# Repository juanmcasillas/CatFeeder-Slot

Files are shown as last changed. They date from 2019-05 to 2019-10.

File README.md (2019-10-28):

# CatFeeder-Slot

This project builds an automatic feeder for cats (or other small animals). The goal is build a complete, DIY solution,
from the fabrication of the container, to software are electronics. The feeder is managed using a web interface, so you
can configure it from your home network. Doubles as WIFI AP (for standalone operation) or WIFI client (for home network
integration).

This project provides:

1. The fabrication of the container. You 3D print the parts using the STL provided.
2. The software to control the feeder.
3. The electronics schemas to connect all the parts. 

<a href="https://youtu.be/_xY0Vlgl6Cg">Demo video on YouTube</a>

# Table Of Contents

1. [Project Features](#project-features)
2. [3D Printing and Assembly](#3d-printing-and-assembly)
    1. [Prototype](#prototype)
    2. [CatFeeder](#catfeeder)
        1. [Part list to print](#part-list-to-print)
        2. [Printing times](#printing-times)
        3. [Assembly](#assembly)
            1. [Mount the pins in the inner case](#mount-the-pins-in-the-inner-case)
            2. [Screw the base to the inner case](#screw-the-base-to-the-inner-case)
            3. [Mount the axis motor and support](#mount-the-axis-motor-and-support)
            4. [Iron the wires to battery holder](#iron-the-wires-to-battery-holder)
            5. [Build the 90 degree wires](#build-the-90-degree-wires)
            6. [Wiring diagram](#wiring-diagram)
            7. [Mount the UNL2003](#mount-the-unl2003)
            8. [Mount the ESP8266](#mount-the-esp8266)
            9. [Mount the cap](#mount-the-cap)

3. [How to install the Software](#how-to-install-the-software)
    1. [Arduino Board Setup](#arduino-board-setup)
    2. [Configuration options](#configuration-options)
    3. [Download the components to the Board](#download-the-components-to-the-board)
        1. [Check for good compilation](#check-for-good-compilation)
        2. [Download the FileSystem to the board](#download-the-filesystem-to-the-board)
        3. [Download the CatFeeder application to the board](#download-the-catfeeder-application-to-the-board)
4. [Configure CatFeeder](#configure-catfeeder)
    1. [Connect to the AP](#connect-to-the-ap)
5. [Using Catfeeder](#using-catfeeder) 
    1. [Calibration](#calibration)
    2. [Configure Schedules](#configure-schedules)
6. [Additional Notes](#additional-notes)

# Project Features

1. Fully printable container, so you can download the project, start your printer, and print all the parts. The STL are 
ready to print, so the orientation and tolerances are configured and tested.
2. Managed using web interface. Catfeeder provides a WWW server that provides the following capabilities:
    * Network configuration. DCHP / Static / AP operation
    * Calibration
    * NTP client, so we manage the current time.
    * Configuration persistence (SPIFFS).
    * Detailed log of Catfeeder's operation, so you can check what happen.
    * Modern HTML / JS interface, AJAX based operation.
    * Easy, flexible schedule configuration for feeding your pets. No limits on this (only the number of slots).
    * Capable of communicate using a Telegram Bot (Experimental).
3. Cheap to build. Based on standard hardware components:
    * ESP8266 Core on an NodeMCU LoLin v3 development board (about 7€)
    * Stepper motor: 28BYJ48 (5 motors about 6€)
    * Stepper motor driver: ULN2003 (5 drivers mounted on development board about 6€)
    * Printed on PLA
    * Some wiring cable (8 wires)
    * 4 allen screws (13mm)
    * 2 allen screws (6mm)
    * Powered on 4xAA batteries (6V)
    * 1 4xAA battery holder (5 holders about 4€)
    * 4 small screws to support the boards to pins
    * 4 pins to build the power connector
4. Easy of operation:
    * Cap is removable so you can clean / add the meal easily.
    * The shape is designed to be "safe" for your cats. They can't bump it.
    * Schedule the meals using the phone or your computer easily.
    * With 1 meal/day, you can serve a full week.
    * Very quiet operation, due the stepper motor.
    * Can be calibrated easily, using the web interface.

# 3D Printing and Assembly

All the parts are designed on Autodesk Inventor 2019. I provide two models, **CatFeeder** the "production" one, and the **Prototype** useful to develop new features, or test things. Printed on 
a Creality Ender-3 Pro, with generic brand PLA. These are the CURA settings for all the parts printed:

* Layer Height: 0.2
* Wall Thickness: 0.8
* Top/Botton Thickness: 0.8
* Top Layers: 4
* Bottom Layers: 4
* Infill: 20%, Lines
* Printing temperature: 195 ºC (for your PLA brand, may vary)
* Build plate temperature: 70 ºC
* Speed: 40 mm/s
* Cooling: Enable
* Fan Speed: 100%
* Enable supports: Everywhere
* Build Plate adhesion: None

## Prototype

This prototype is not usable to feed pets, buts prints fast, and is used to check some mechannical interfaces (axis, motor coupling, etc.) The prototype is an easy asembly, build from three printed parts:

* Hardware/3DPrinting/Prototype/floor.stl
* Hardware/3DPrinting/Prototype/mottor_support.stl
* Hardware/3DPrinting/Prototype/upper.stl

You also need:

* 6 female-female pin-to-pin cables (4 for motor wires, 1 for vcc, 1 for ground)
* 4 AA batteries
* A battery holder with two male pin soldered (to enable the connection)
* A ESP8266 Board
* Mini-USB Cable (to power the ESP8266 and check the serial debug)

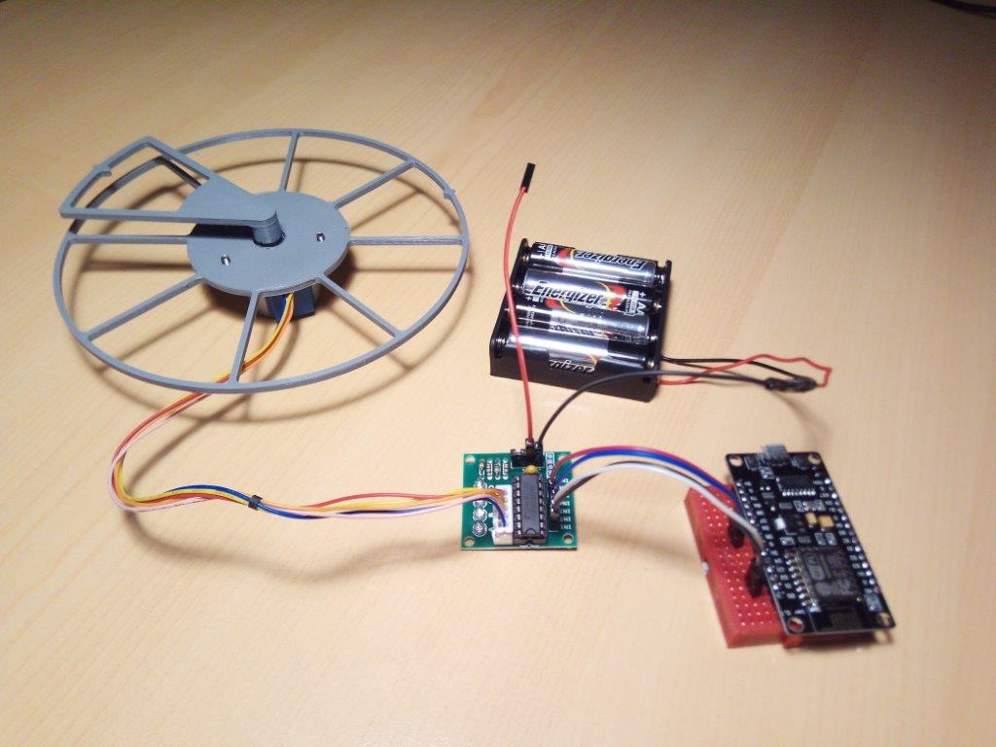
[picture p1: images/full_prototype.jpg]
  

## CatFeeder

This is the production-ready CatFeeder parts. CatFeeder has a diameter of **190mm**, and **650** of height. Each slots size **72mm x 90mm**. It takes some time to print, so be patient.
See the following diagram for more detail about measures.

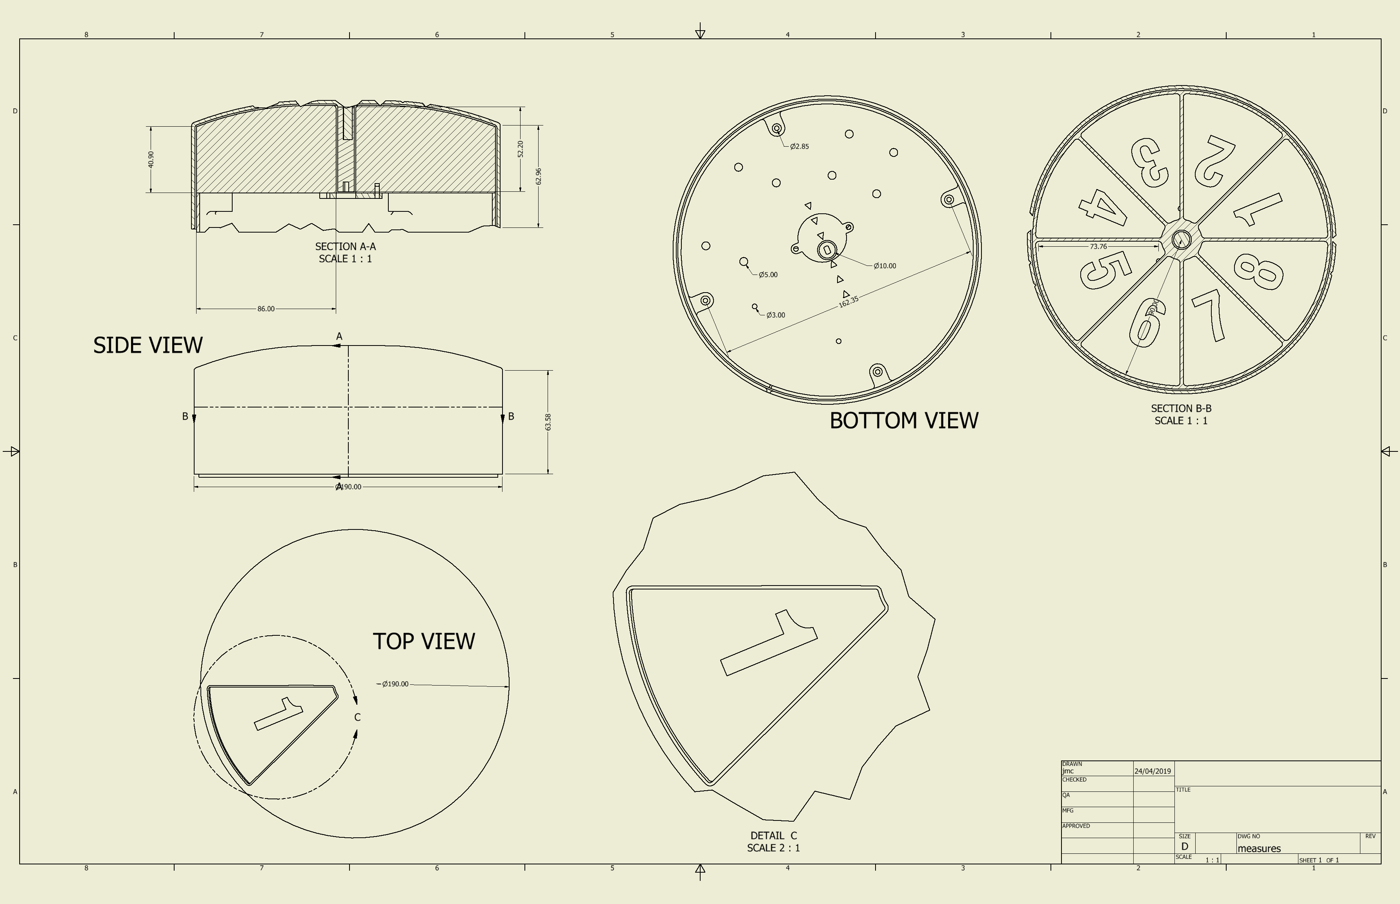
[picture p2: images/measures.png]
  

### Part List to print

You need to print this files (included in the Repo):

* Hardware/3DPrinting/CatFeeder/1x_axis.stl 
* Hardware/3DPrinting/CatFeeder/1x_motor_support.stl  
* Hardware/3DPrinting/CatFeeder/1x_base.stl
* Hardware/3DPrinting/CatFeeder/1x_cap.stl
* Hardware/3DPrinting/CatFeeder/1x_inner_case.stl
* Hardware/3DPrinting/CatFeeder/2x_separator_battery.stl
* Hardware/3DPrinting/CatFeeder/8x_separator.stl

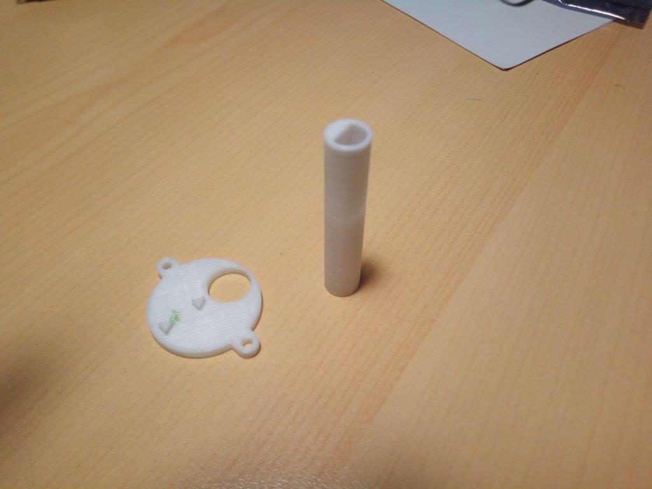
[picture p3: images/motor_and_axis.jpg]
 
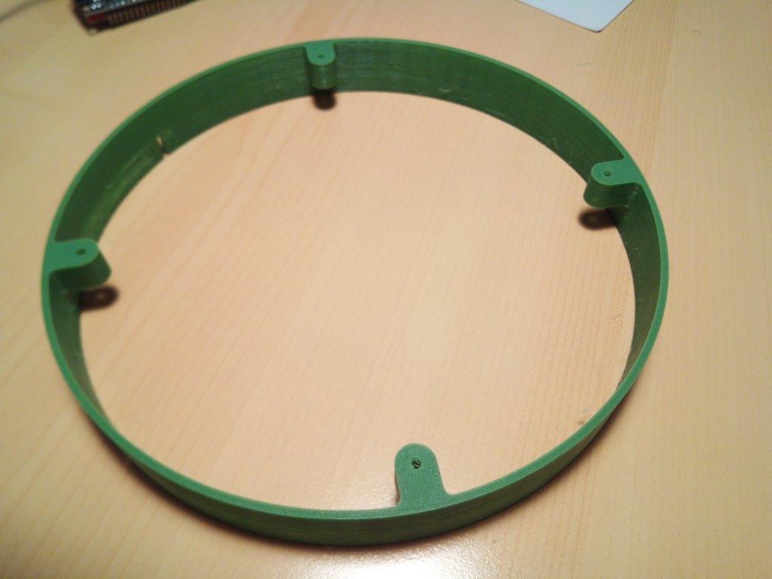
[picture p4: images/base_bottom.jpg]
 
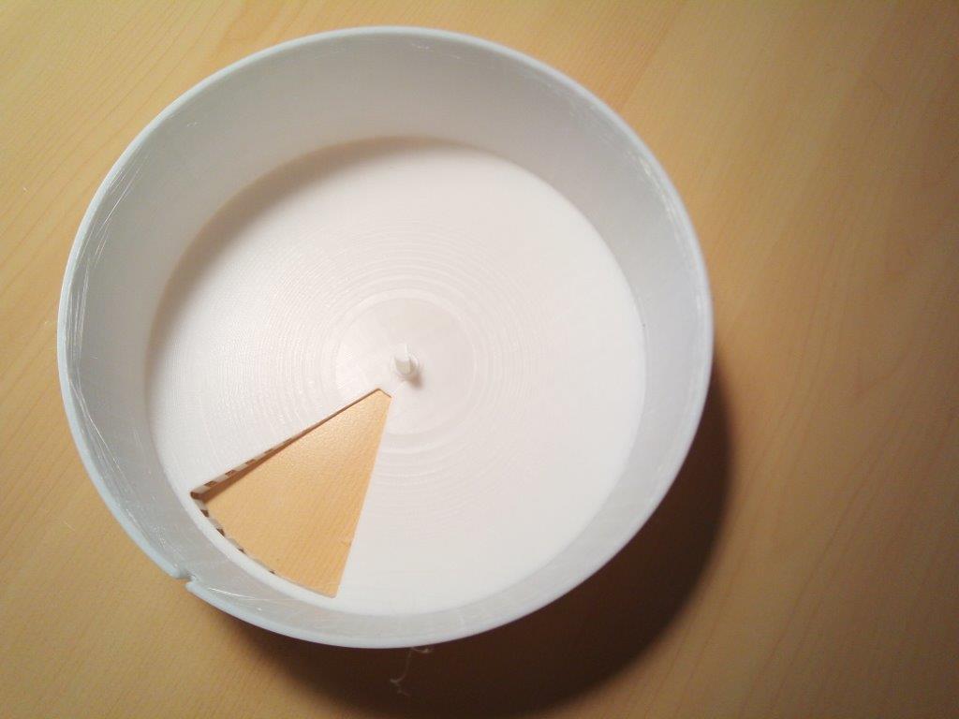
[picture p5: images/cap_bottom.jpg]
 
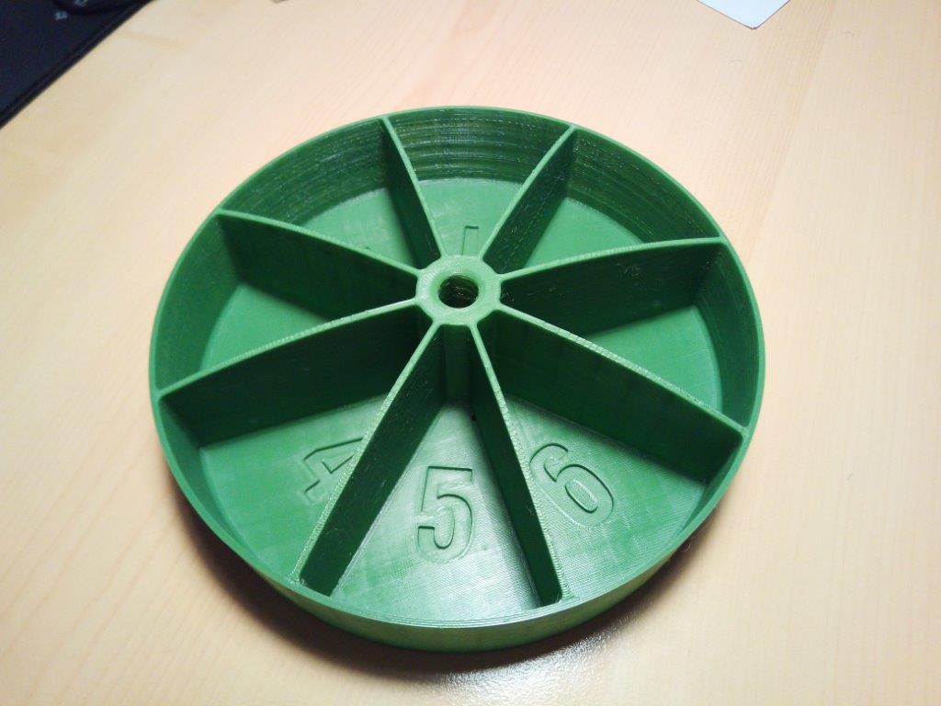
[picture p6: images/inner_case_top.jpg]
 
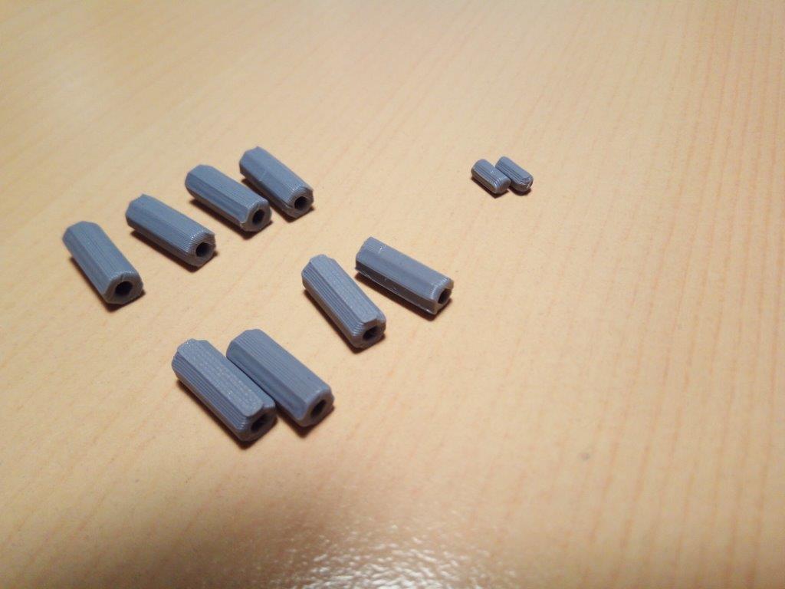
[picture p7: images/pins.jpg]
 

### Printing times

|part name  |cuantity|color|printing time|
|---|---|-----|---:|
|motor axis |1 |white| 00:45|
|base |1 |green| 02:30|
|cap |1 |white| 14:38|
|inner case |1 |green| 16:15|
|motor support |1 |white| 00:30|
|separator_battery|2 |grey | 00:05|
|separator |8 |grey | 00:10|

### Assembly

To assemble the CatFeeder, you need the following:

* All the parts printed
* ESP8266 Core on an NodeMCU LoLin v3 development board
* Stepper motor: 28BYJ48
* Stepper motor driver: ULN2003
* Some wiring cable (10 wires)
* 4 allen screws (13mm)
* 2 allen screws (6mm)
* 4xAA batteries (6V)
* 1 4xAA battery holder
* 1 Micro USB cable to download the firmware
* An allen driver to screw the allen screws (nº 3)
* An Iron to solder the battery holder wires and build the 90 degree wires
* 4 small screws to support the boards to pins

#### Mount the pins in the inner case

Parts:
* Separators (8 big, 2 small)
* Inner Case (bottom side)

Push the pins (separators) in their holes to support the boards. The two small ones are the battery separator (2mm) and the 8 are the ULN2003 holder and ESP9266 holder, that fits in the big holes.
Push gently, and if you found too much resistence, file them lightly using a sharp knife. Also you can glue the pins to the base, but it shouldn't be needed.

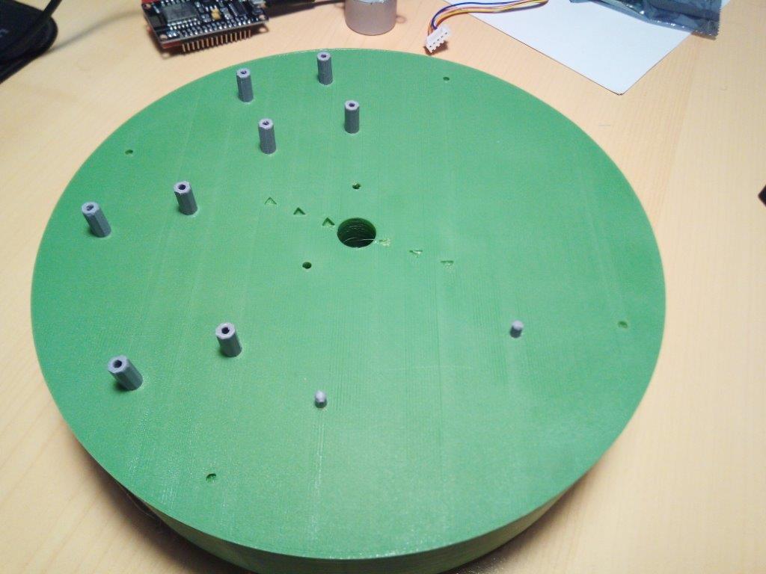
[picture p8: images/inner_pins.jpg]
 

#### Screw the base to the inner case

Parts:
* Inner Case
* Base
* 4 Screws (10mm, allen) 

Using the 4 long screws, screw the base to the inner case. File lightly the holes to ensure smooth fit.

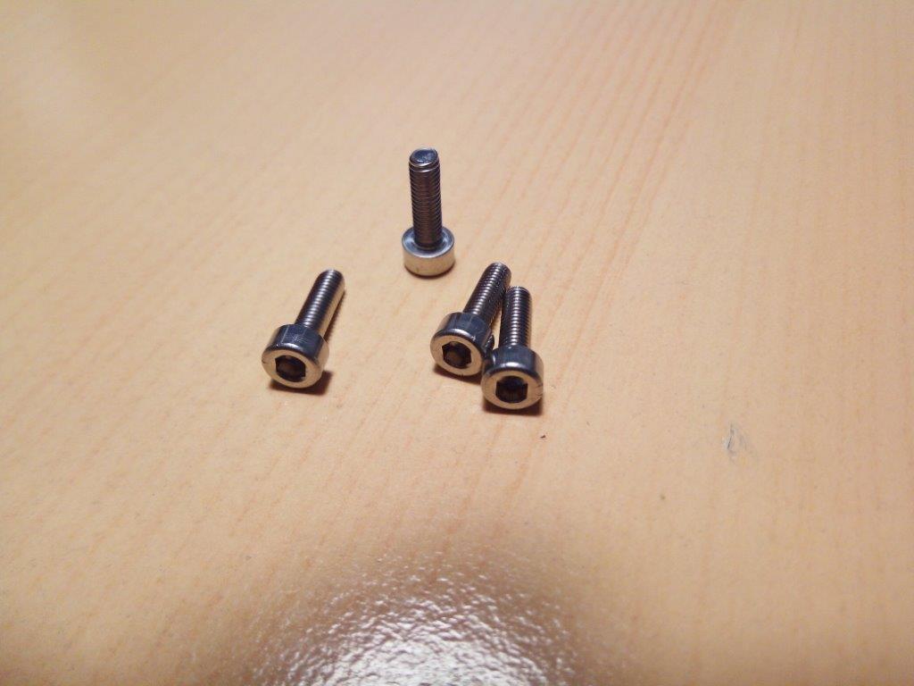
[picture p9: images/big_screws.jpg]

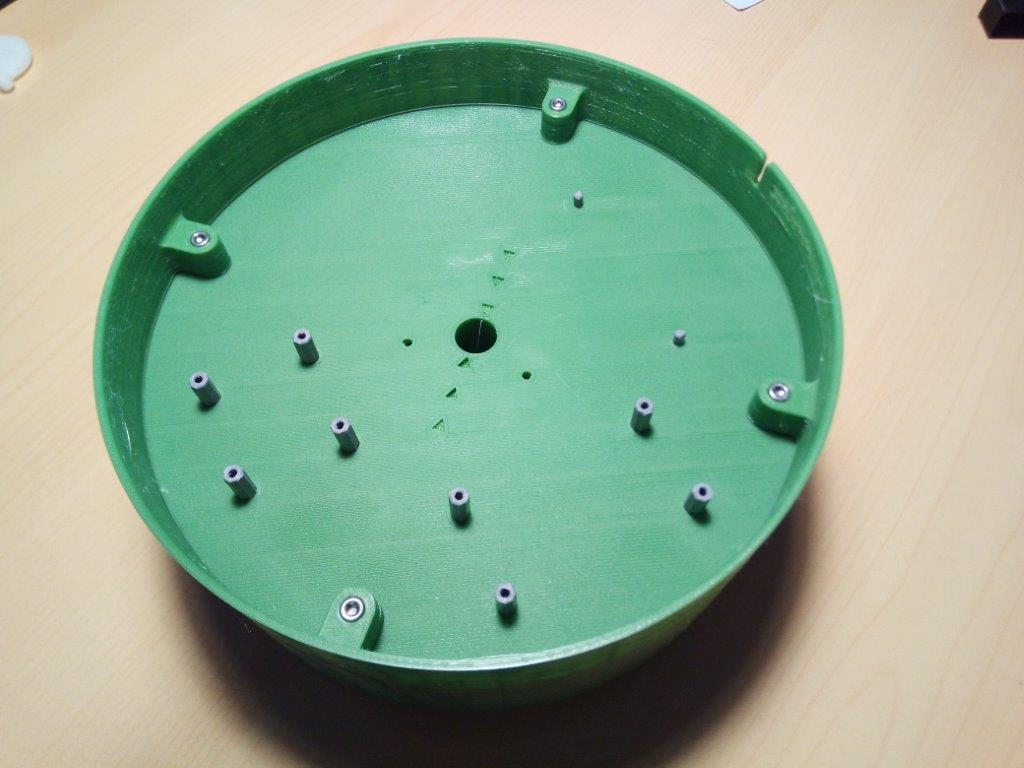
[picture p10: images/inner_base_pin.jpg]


#### Mount the axis motor and support

Parts:
* Motor Axis
* Motor Support
* 2 Screws (6mm, allen)

Push gently the motor into the axis. The axis (long part) has two pockets. One big, one small. In the photo you will see the big one, used to hold the cap. Push firmly but not to hard. It should be fitted
snugly. 

Now, get the motor support, and align it with the inner base (bottom) The protuding triangles are designed to be fitted in the triangle pockets in the inner case. Once fitted the support, screw the motor
to the inner case using the small screws. The support, the motor and the axis only have one way to be mounted.


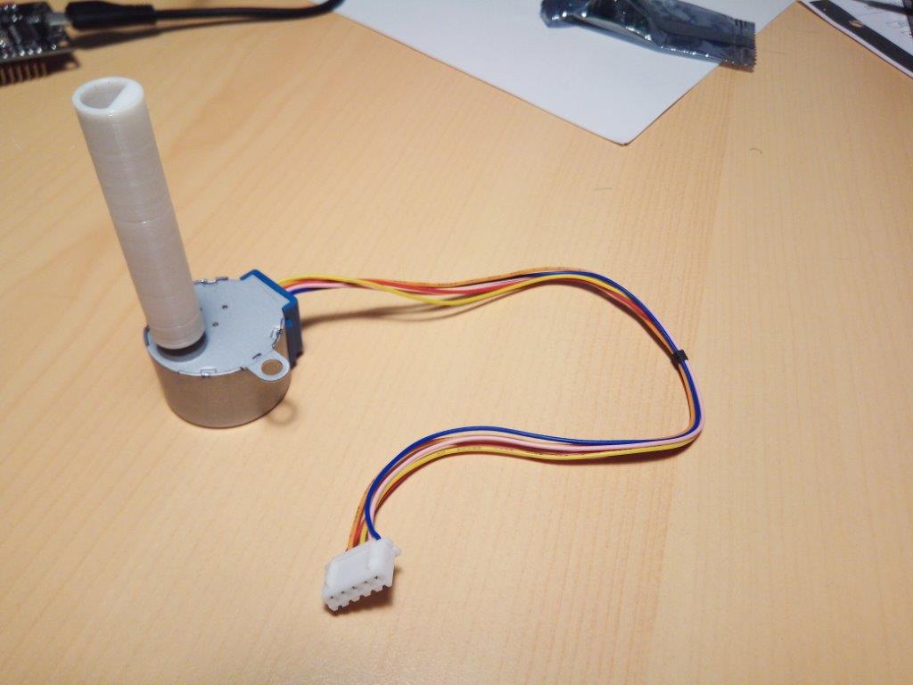
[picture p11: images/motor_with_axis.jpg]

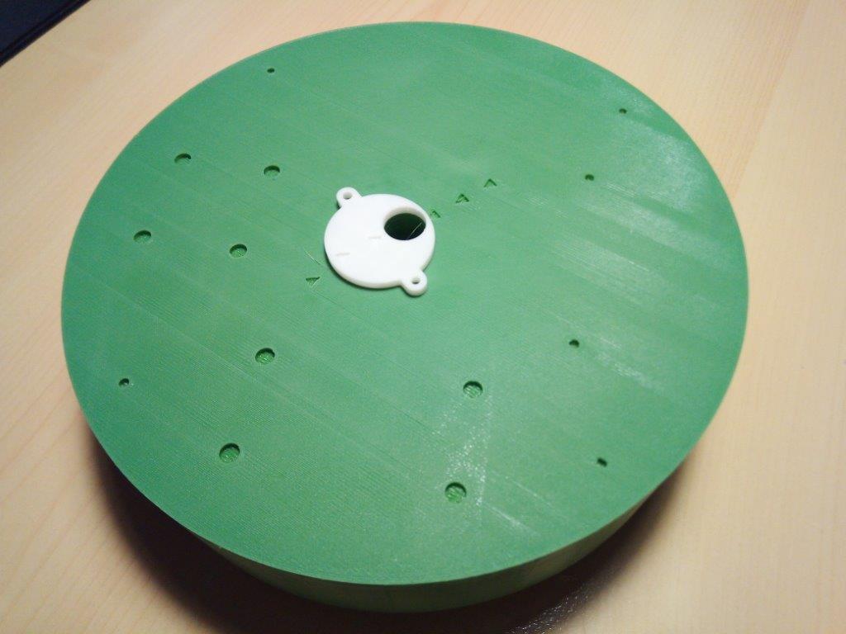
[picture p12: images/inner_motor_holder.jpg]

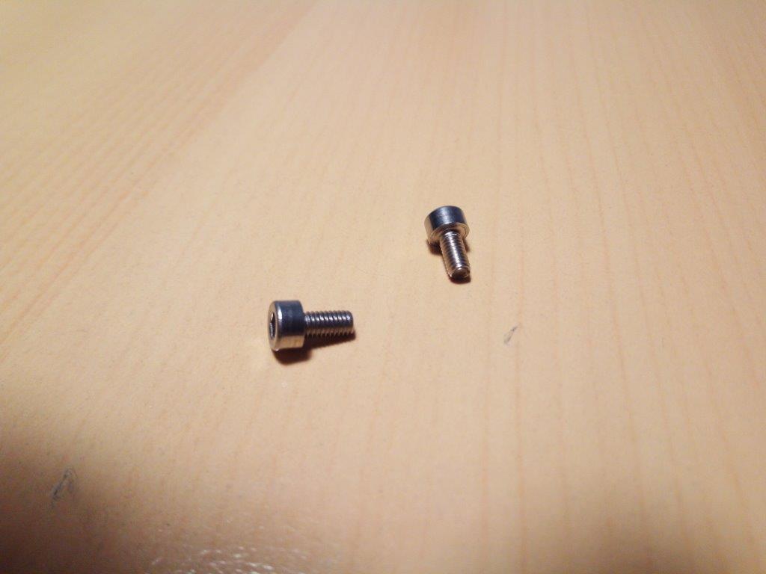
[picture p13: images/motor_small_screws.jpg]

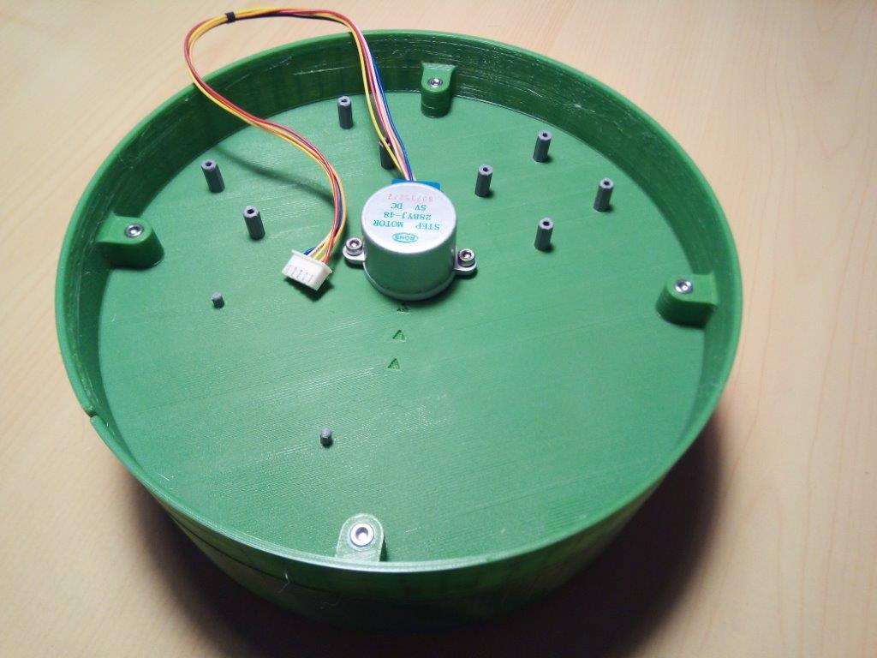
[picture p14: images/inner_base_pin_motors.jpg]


#### Iron the wires to battery holder

Parts:
* Battery Holder
* Two wires (about 10cm each one)
* 4 pins to build the connector
* Iron

First of all, we need to "build" a connector for the power. Get a pin strip as the photo, and split two pairs of pins. Stack them, and iron the pins
together using the wires. You will get something like the connector in the photo.  Then, iron the wires to the battery holder. 
I usually iron the *red* one to the VCC (+) and the *black* to the GND (-).

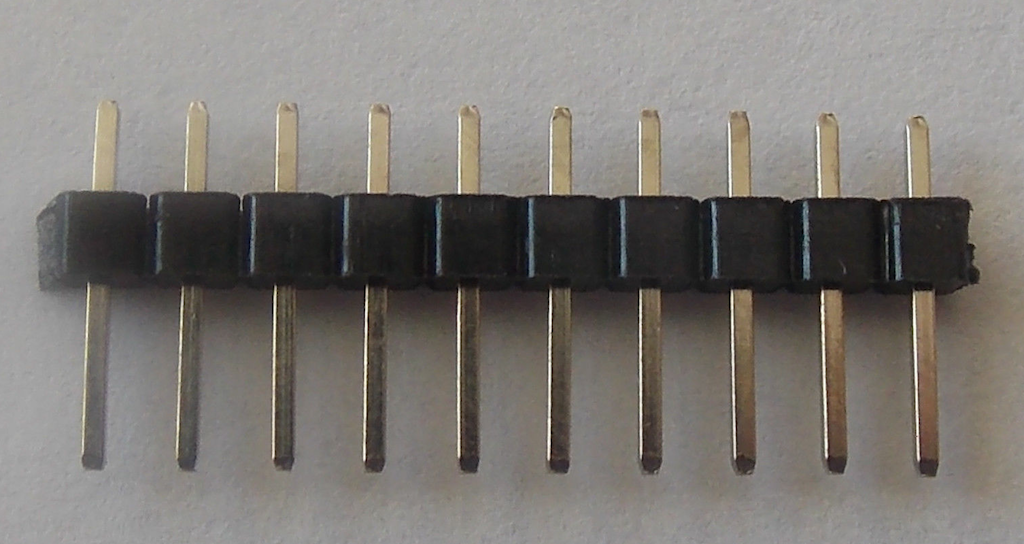
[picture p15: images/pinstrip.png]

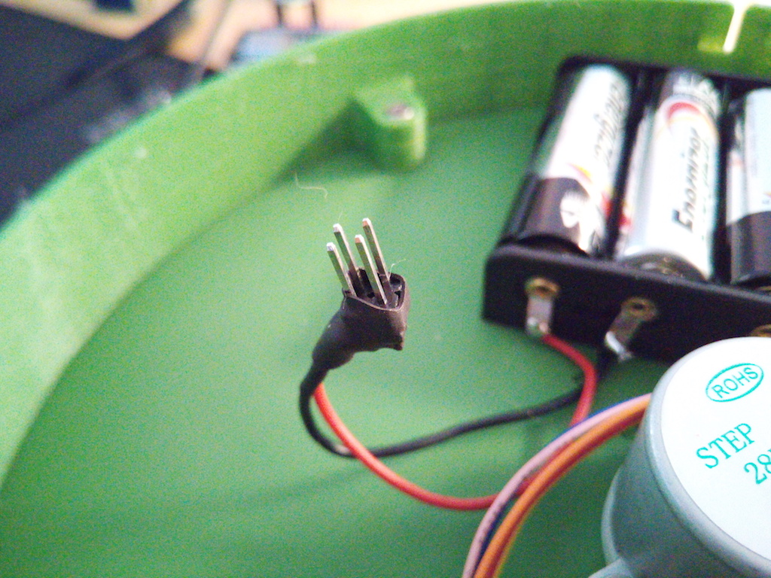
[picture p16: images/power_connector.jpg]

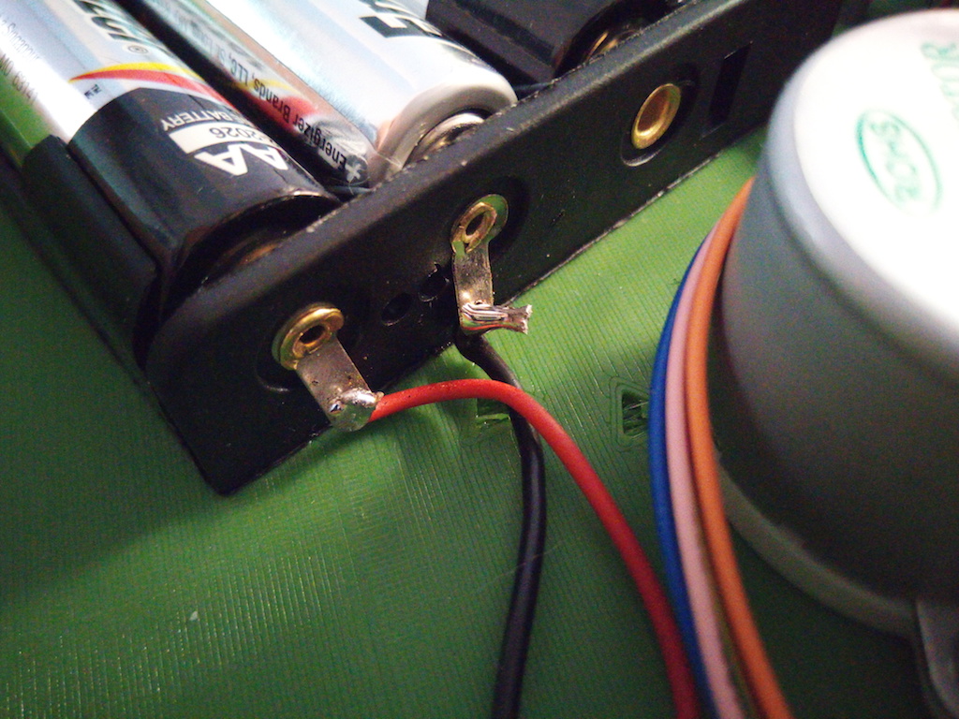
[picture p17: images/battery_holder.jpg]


#### Build the 90 degree wires

Parts:
* Simple female-female connection wires (10)
* Iron
* plier

I want to get a low-profile cat feeder, so I ended using 90 degrees cables to connect the ESP8266 and the UNL2003 motor driver, along the power supply. I get a standard
female-female connection wire, removing the plastic cap (a needle or sharp cutter is useful to extract the plastic cap), add some thermoretractile (while the pin is still
straight) and them, using the pliers, bend the end point to 90 degree. Apply some heat, and you have a 90-degree connection cable done. Repeat 10 times (4 wires for 
motor signals, 2 for power the ESP8266, 2 for power the UNL2003).

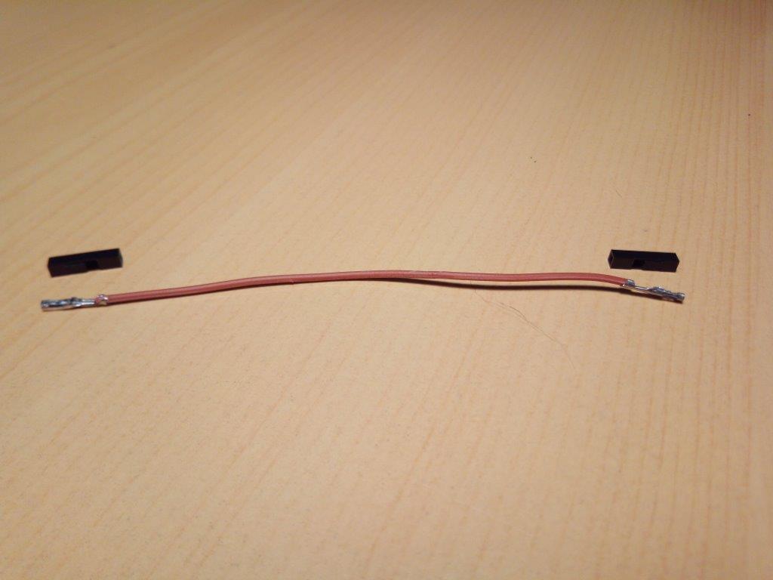
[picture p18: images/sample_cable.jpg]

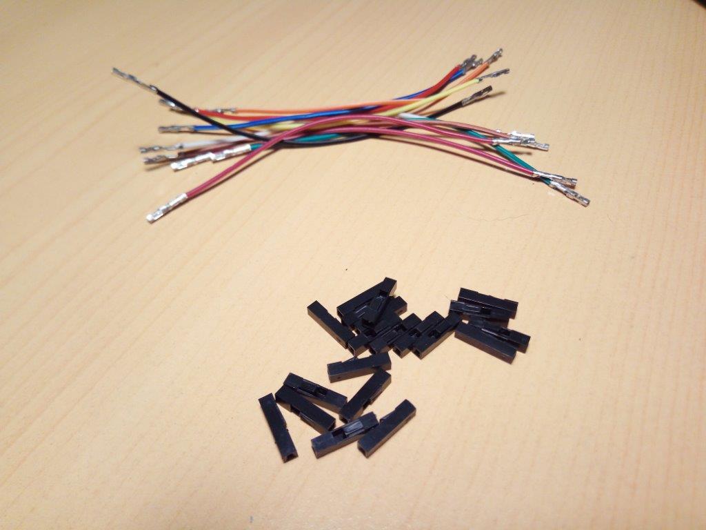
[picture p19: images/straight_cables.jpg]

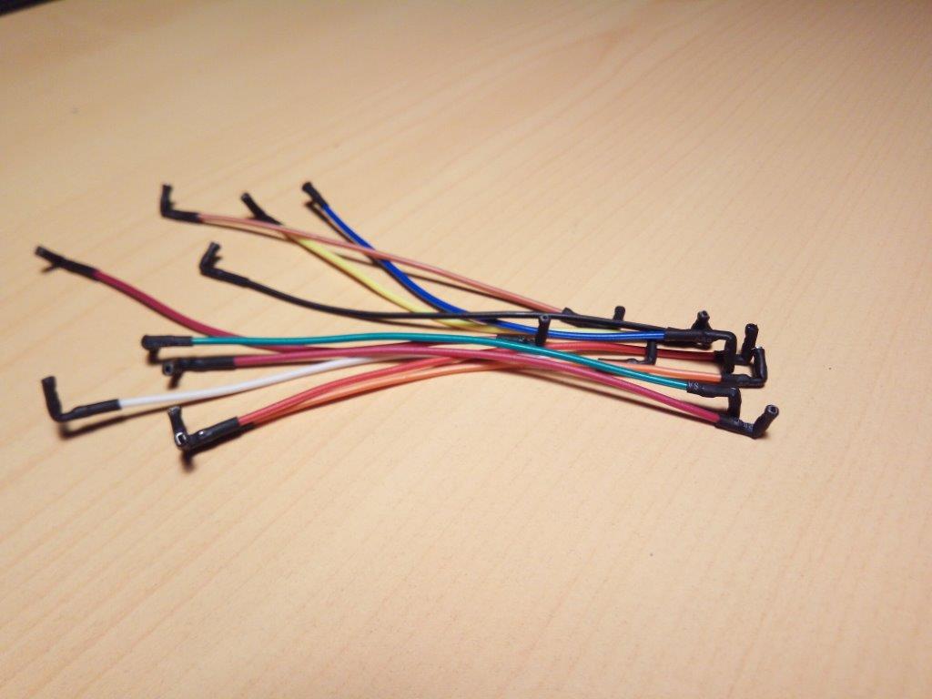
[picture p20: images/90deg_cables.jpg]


#### Wiring diagram

Wiring is easy. Just use the following diagram to connect the wires between power, ESP8266, UNL2003 and the stepper motor. I power the ESP8266 using 6V (4x1.5V) using the
voltage regulator provided by the development board. See the subsections about UNL2003 and ESP8266 for detailed photos. 

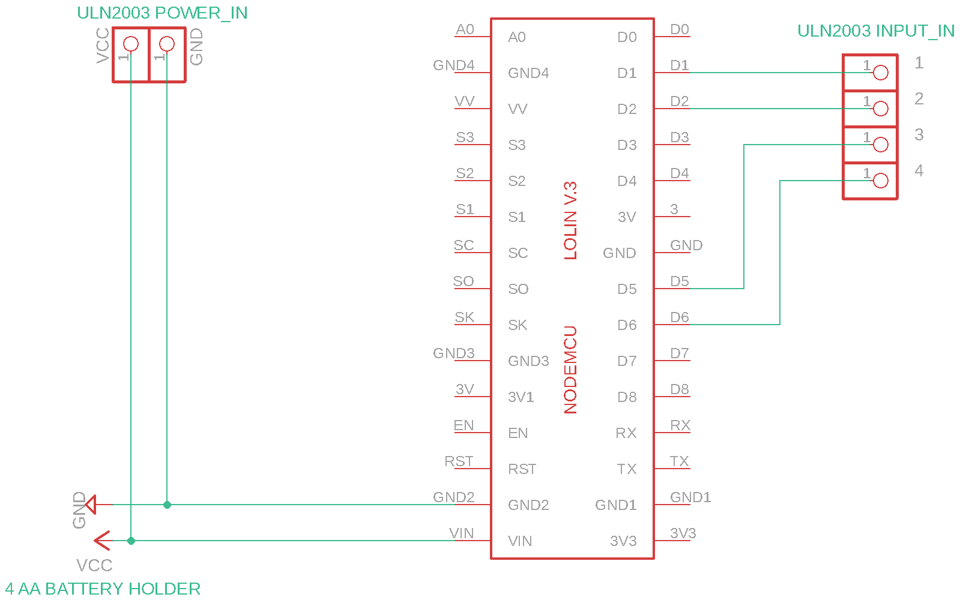
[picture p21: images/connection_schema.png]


#### Mount the UNL2003 

Parts:
* Inner case
* UNL2003 Motor Driver
* 6 wires (4 for signals, 2 for power)
* Motor connector
* 2 small screws

Put the UNL2003 in their separators, and screw it to them using the small screws. I get these screws from iside a VHS video recorder found in the garbage. Plug in the
motor connector in the white connector holder (it has only one valid position to insert it). Last, connect the wires using the following table.

|UNL2003 Name|Color |ESP8266 PIN|
|---|---|---|
|IN1 |Yellow|D1 |
|IN2 |Orange|D2 |
|IN3 |Grey  |D5 |
|IN4  |Blue  |D6 |
|- |White |*power connector black*|  
|+ |Red |*power connector red*|

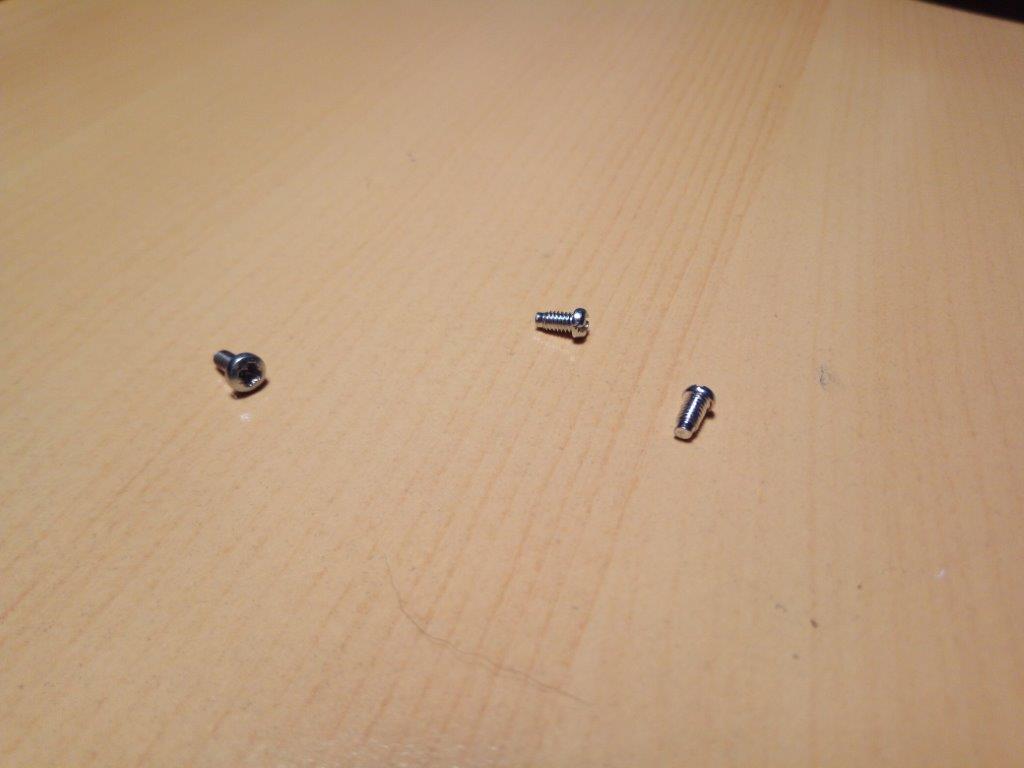
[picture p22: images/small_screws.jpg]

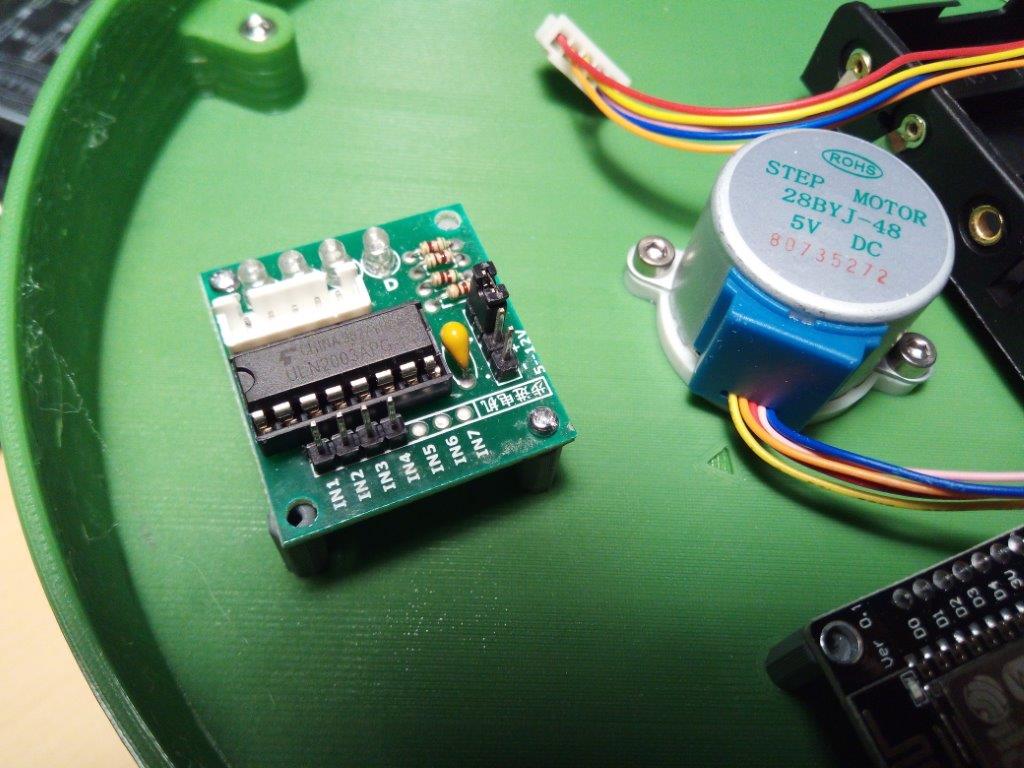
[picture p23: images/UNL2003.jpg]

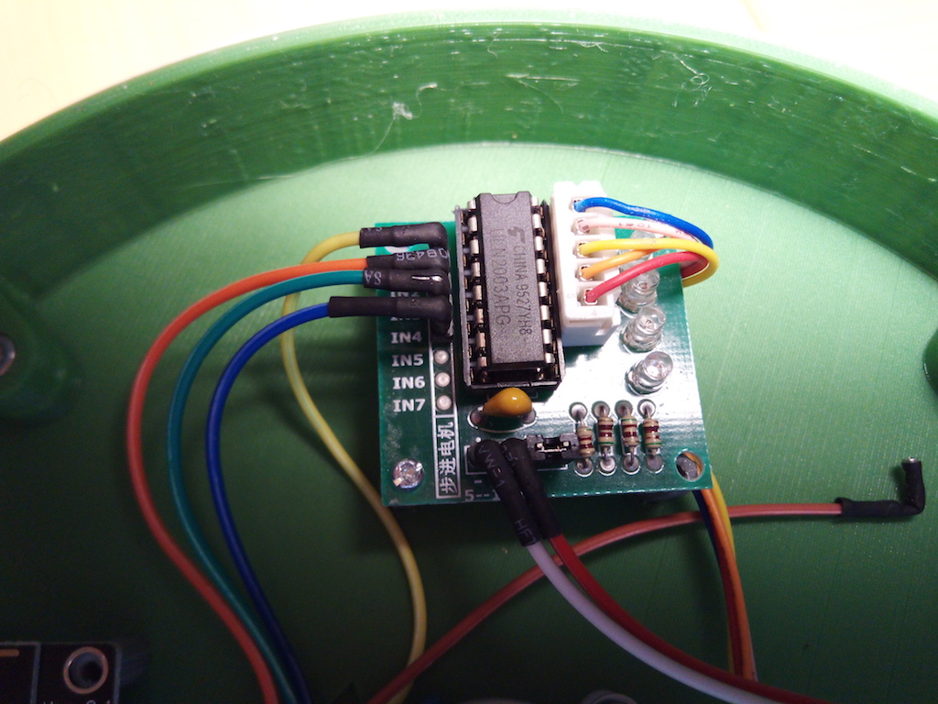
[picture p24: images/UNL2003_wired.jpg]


#### Mount the ESP8266 

Parts:
* Inner case
* ESP8266 
* 4 wires coming from UNL2003
* 2 wires for power
* 2 small screws
* Micro-USB cable

First of all, connect the wires coming from UNL2003 using the previous table. Connect the power cables to the `GND2` (black wire) and `VIN` (red wire) pins, and screw 
it to the separators. Last, plug all the power wires to the battery holder connector. You shold have all connected and ready to go. Don't forget to plug the Micro-USB
cable to the ESP8266 in order to download the filesystem and firwware. The extra, unpluged wire in the photo is due a some test I was doing. Don't take it in mind.

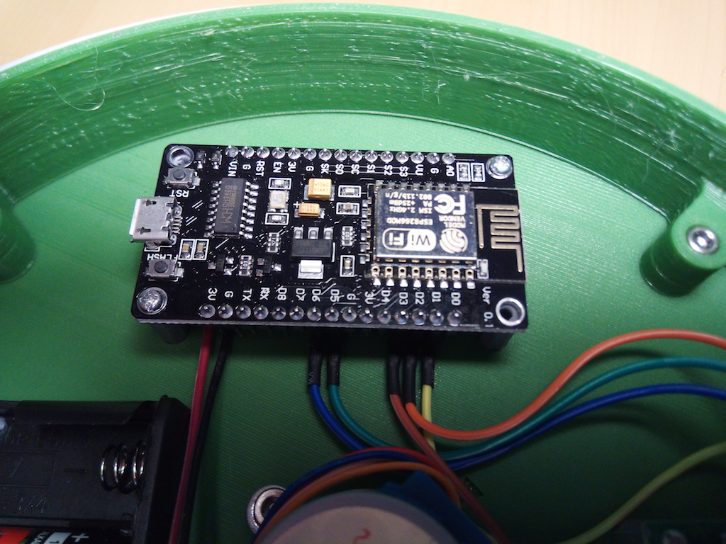
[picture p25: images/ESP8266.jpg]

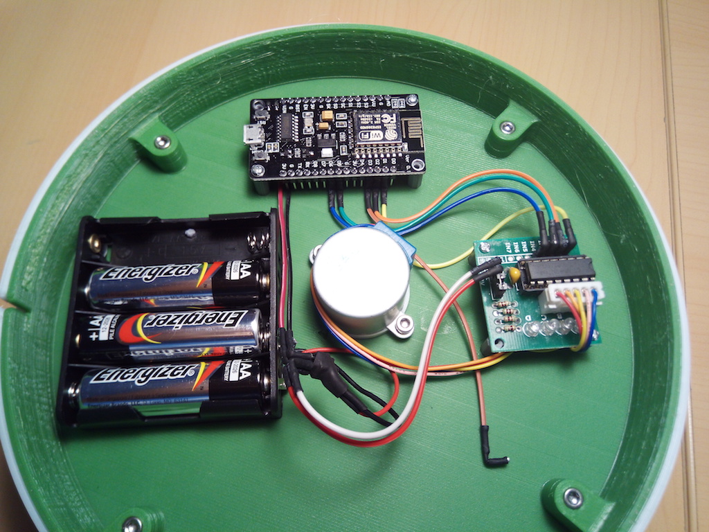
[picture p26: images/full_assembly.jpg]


#### Mount the cap

Parts:
* Cap
* Inner case fully assembled

First of all, remove all the support from the top of the cap. Use a sharp cutter. The cap has an axis that fits in the motor axis. This allows the cap to be removed to
put the food, clean the inner case, etc. The cap fits easily in the axis holder. You are done!.

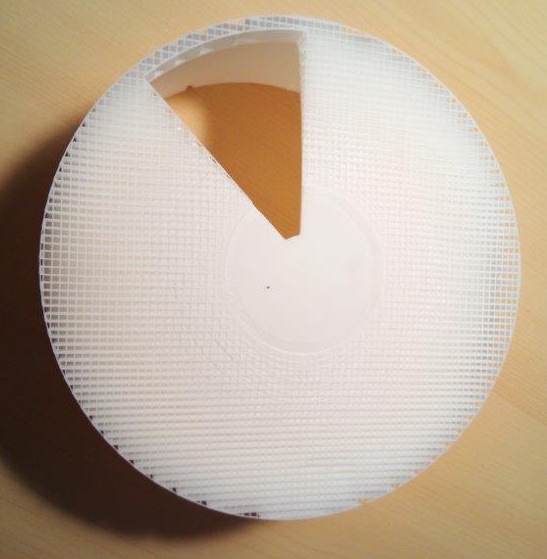
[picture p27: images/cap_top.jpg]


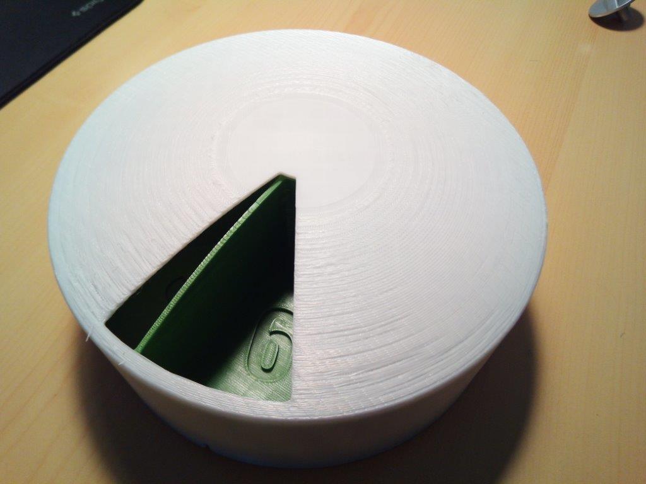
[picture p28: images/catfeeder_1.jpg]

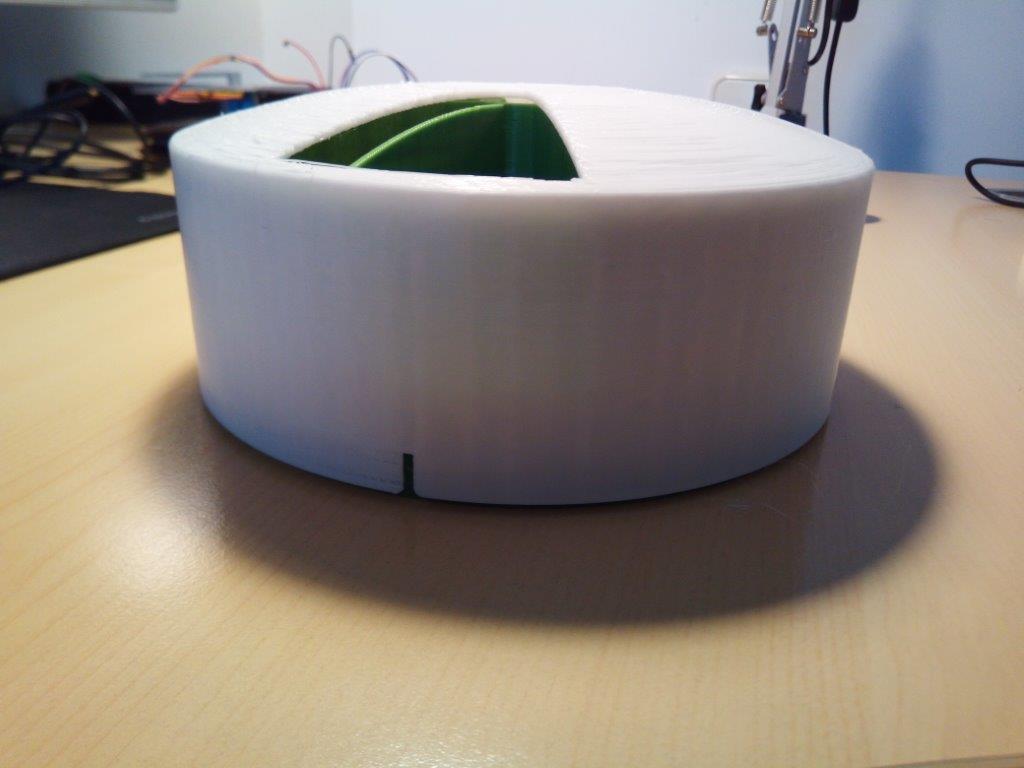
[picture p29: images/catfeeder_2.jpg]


# How to install the Software

CatFeeder uses [FSBrowserNG](https://github.com/gmag11/FSBrowserNG) as webserver. I forked it, to include some new functionality and fix some `delay()` calls that can't be used. You need the following libraries installed in your Arduino `libraries` folder.

* [my FSBrowserNG's fork](https://github.com/juanmcasillas/FSBrowserNG). See [the original page](https://github.com/gmag11/FSBrowserNG) for more info. Depends on:
    * [ArduinoJson-5.x](https://github.com/bblanchon/ArduinoJson/tree/5.x) (the 5.x branch)
    * [ESPAsyncTCP](https://github.com/me-no-dev/ESPAsyncTCP)
    * [ESPAsyncWebServer](https://github.com/me-no-dev/ESPAsyncWebServer)
    * [NtpClient](https://github.com/arduino-libraries/NTPClient)
    * [Time](https://github.com/PaulStoffregen/Time)
* [my Universal-Arduino-Telegram-Bot's fork](https://github.com/juanmcasillas/Universal-Arduino-Telegram-Bot). See [the original page](https://github.com/witnessmenow/Universal-Arduino-Telegram-Bot) for more info.

Then, get the [CatFeeder Repo](https://github.com/juanmcasillas/CatFeederCircular) and compile it using the Arduino IDE.

## Arduino Board Setup

I use a *NodeMCU LoLin v.3 ESP8266* board. You need some things in Arduino IDE in order to work:

* First install the serial driver, if not installed before, for your platform [CH340G Driver](http://www.wch.cn/download/CH341SER_EXE.html)

Then add ESP8266 aditional library:
* Go to `Preferences`, add in `Additional Board Manager URLs` the following URL: [http://arduino.esp8266.com/stable/package_esp8266com_index.json](http://arduino.esp8266.com/stable/package_esp8266com_index.json)
* Restart The Arduino IDE.
* Go to `Tools->Board->Board Manager` and search `ESP8266 by ESP8266 Community` library and install it (I use version `2.5.0`)
* Install the ESP8266FS Flash filesystem tools form Arduino. Uncompress [package](https://github.com/esp8266/arduino-esp8266fs-plugin/releases/download/0.1.3/ESP8266FS-0.1.3.zip) inside `C:\Software\Arduino\tools`
* Install Exception Decoder ESP8266. Not really needed to install the software, but can help you to troubleshoot some things if fail. Uncompress [package](https://github.com/me-no-dev/EspExceptionDecoder/releases/download/1.1.0/EspExceptionDecoder-1.1.0.zip) inside `C:\Software\Arduino\tools`
* Restart the Arduino IDE.

Now, You have to configure the Board options:

* Board: `NodeMCU 1.0 (ESP-12E Module)`
* Upload Speed: `921600` (If you can't connect at this speed, check the cable or select a lower speed)
* CPU Freq: `80 MHz`
* Flash Size: `4M (2M SPIFFS)`. This is importart. If you don't do select that, you can't flash the FileSystem.
* Debug port: `Disabled`
* Debug Level: `None`
* IWIP Variant: `v2 Lower Memory`
* VTables: `Flash`
* Exceptions: `Disabled`
* Erase Flash: `Only Sketch`
* Port: Your USB port.
* Programmer: `AVRISP mkII`

## Configuration options

in `catfeeder.h` you find the following `defines`:
* `#define CATFEEDER_SLOTS 8` number of slots. If you use the provided STL, leave in `8`
* `String CATFEEDER_CONFIG_FILE =  "/catfeeder.json"`. The configuration options.
* `String LOGGER_FILE = "/catfeeder.log". The log file where things are stored.

in `motorstepper.h` you find the pin-to-wire mapping:
* `const int motorPin1 = D1;   // D1  (GPIO14)      IN1     black`
* `const int motorPin2 = D2;   // D2  (GPIO12)      IN2     white`
* `const int motorPin3 = D5;   // D5  (GPIO13)      IN3     blue`  
* `const int motorPin4 = D6;   // D6  (GPIO15)      IN4     red` 

## Download the components to the Board

### Check for good compilation

 First of all, open `catfeedercircular.ino` file in *Arduino IDE* and issue a `Verify` to check that everything compiles (libraries, and so on). When you have a valid compilation, then you should have a log output like this:

 ```
Using library ESP8266WiFi at version 1.0 in folder: /Users/assman/Library/Arduino15/packages/esp8266/hardware/esp8266/2.5.0/libraries/ESP8266WiFi 
Using library Time at version 1.5 in folder: /Archive/Src/Arduino/libraries/Time 
Using library NtpClient at version 2.5.1 in folder: /Archive/Src/Arduino/libraries/NtpClient 
Using library ESPAsyncTCP at version 1.2.0 in folder: /Archive/Src/Arduino/libraries/ESPAsyncTCP 
Using library ESPAsyncWebServer at version 1.2.0 in folder: /Archive/Src/Arduino/libraries/ESPAsyncWebServer 
Using library ESP8266mDNS at version 1.2 in folder: /Users/assman/Library/Arduino15/packages/esp8266/hardware/esp8266/2.5.0/libraries/ESP8266mDNS 
Using library Ticker at version 1.0 in folder: /Users/assman/Library/Arduino15/packages/esp8266/hardware/esp8266/2.5.0/libraries/Ticker 
Using library ArduinoOTA at version 1.0 in folder: /Users/assman/Library/Arduino15/packages/esp8266/hardware/esp8266/2.5.0/libraries/ArduinoOTA 
Using library ArduinoJson at version 5.13.5 in folder: /Archive/Src/Arduino/libraries/ArduinoJson 
Using library FSBrowserNG at version 1.0.0 in folder: /Archive/Src/Arduino/libraries/FSBrowserNG 
Using library Hash at version 1.0 in folder: /Users/assman/Library/Arduino15/packages/esp8266/hardware/esp8266/2.5.0/libraries/Hash 
Using library Universal-Arduino-Telegram-Bot at version 1.1.0 in folder: /Archive/Src/Arduino/libraries/Universal-Arduino-Telegram-Bot 
/Users/assman/Library/Arduino15/packages/esp8266/tools/xtensa-lx106-elf-gcc/2.5.0-3-20ed2b9/bin/xtensa-lx106-elf-size -A /var/folders/cc/0xwh_8tn7xdf8834vtcvvlt00000gn/T/arduino_build_599193/catfeedercircular.ino.elf
Sketch uses 540636 bytes (51%) of program storage space. Maximum is 1044464 bytes.
Global variables use 40004 bytes (48%) of dynamic memory, leaving 41916 bytes for local variables. Maximum is 81920 bytes.
```

If you have some error, it has been a missing library, probably.

### Download the FileSystem to the board

Go to `Tools->ESP8266 Sketch Data Upload`. This put all the files in the flash partition of the board.

```
[SPIFFS] data   : /Archive/Src/CatFeederCircular/Software/catfeedercircular/data
[SPIFFS] size   : 2028
[SPIFFS] page   : 256
[SPIFFS] block  : 8192
/cal.png
/edit.html
/f1.png
/f2.png
/f3.png
/f4.png
/f5.png
/f6.png
/f7.png
/f8.png
/favicon.ico
/in.png
/index.html
/logo.png
/majax.js
/md5.js
/net.html
/net_auth.html
/net_config.html
/net_ntp.html
/out.png
/pickr.css
/pickr.js
/s.css
/schedule.html
/stats.html
/sys.html
/sys_bot.html
/sys_cal.html
/sys_config.html
/sys_info.html
/sys_reboot.html
/sys_update.html
[SPIFFS] upload : /var/folders/cc/0xwh_8tn7xdf8834vtcvvlt00000gn/T/buildb100809d879243ffa08dcd83fbd33c73.spiffs/catfeedercircular.spiffs.bin
[SPIFFS] reset  : nodemcu
[SPIFFS] port   : /dev/cu.wchusbserial1a140
[SPIFFS] speed  : 921600
[SPIFFS] address: 0x200000

warning: serialport_set_baudrate: baud rate 921600 may not work
Uploading 2076672 bytes from /var/folders/cc/0xwh_8tn7xdf8834vtcvvlt00000gn/T/buildb100809d879243ffa08dcd83fbd33c73.spiffs/catfeedercircular.spiffs.bin to flash at 0x00200000
................................................................................ [  3% ]
................................................................................ [  7% ]
................................................................................ [ 11% ]
................................................................................ [ 15% ]
................................................................................ [ 19% ]
................................................................................ [ 23% ]
................................................................................ [ 27% ]
................................................................................ [ 31% ]
................................................................................ [ 35% ]
................................................................................ [ 39% ]
................................................................................ [ 43% ]
................................................................................ [ 47% ]
................................................................................ [ 51% ]
................................................................................ [ 55% ]
................................................................................ [ 59% ]
................................................................................ [ 63% ]
................................................................................ [ 67% ]
................................................................................ [ 71% ]
................................................................................ [ 74% ]
................................................................................ [ 78% ]
................................................................................ [ 82% ]
................................................................................ [ 86% ]
................................................................................ [ 90% ]
................................................................................ [ 94% ]
................................................................................ [ 98% ]
............................             
```

### Download the CatFeeder application to the board

After that, you have all the files in the flash, and the last step to get the thing working is Download the CatFeeder sketch. Before this, If you want to 
comment out the debug output, you should edit `FSWebServerLib.h:24` and uncomment the following line:

```
// #define RELEASE  // Comment to enable debug output
```

I recommend you *leave* the log enabled, so you can check that everything starts, the mac address, etc. Ok, it's time to download the sketch. 
If you upload the sketch from Arduino IDE, you should see something like this in the output window:

```
/Users/assman/Library/Arduino15/packages/esp8266/tools/xtensa-lx106-elf-gcc/2.5.0-3-20ed2b9/bin/xtensa-lx106-elf-size -A /var/folders/cc/0xwh_8tn7xdf8834vtcvvlt00000gn/T/arduino_build_599193/catfeedercircular.ino.elf
Sketch uses 540684 bytes (51%) of program storage space. Maximum is 1044464 bytes.
Global variables use 40004 bytes (48%) of dynamic memory, leaving 41916 bytes for local variables. Maximum is 81920 bytes.
warning: serialport_set_baudrate: baud rate 921600 may not work
Uploading 544832 bytes from /var/folders/cc/0xwh_8tn7xdf8834vtcvvlt00000gn/T/arduino_build_599193/catfeedercircular.ino.bin to flash at 0x00000000
................................................................................ [ 15% ]
................................................................................ [ 30% ]
................................................................................ [ 45% ]
................................................................................ [ 60% ]
................................................................................ [ 75% ]
................................................................................ [ 90% ]
.....................................................                            [ 100% ]
```

Now, open the `Serial Monitor` window you will see the debug information and some useful stuff:
 
```
CatFeeder: Failed to open config file /catfeeder.json
AP Enable = 0
FS File: /cal.png, size: 36.13KB
FS File: /edit.html, size: 24.49KB
FS File: /f1.png, size: 43.08KB
FS File: /f2.png, size: 44.35KB
FS File: /f3.png, size: 44.04KB
FS File: /f4.png, size: 42.99KB
FS File: /f5.png, size: 43.31KB
FS File: /f6.png, size: 43.71KB
FS File: /f7.png, size: 42.28KB
FS File: /f8.png, size: 42.81KB
FS File: /favicon.ico, size: 1.12KB
FS File: /in.png, size: 139.03KB
FS File: /index.html, size: 2.03KB
FS File: /logo.png, size: 15.75KB
FS File: /majax.js, size: 5.07KB
FS File: /md5.js, size: 19.97KB
FS File: /net.html, size: 1.14KB
FS File: /net_auth.html, size: 4.13KB
FS File: /net_config.html, size: 6.39KB
FS File: /net_ntp.html, size: 6.72KB
FS File: /out.png, size: 59.51KB
FS File: /pickr.css, size: 14.78KB
FS File: /pickr.js, size: 45.21KB
FS File: /s.css, size: 4.56KB
FS File: /schedule.html, size: 5.50KB
FS File: /stats.html, size: 1.65KB
FS File: /sys.html, size: 1.43KB
FS File: /sys_bot.html, size: 2.62KB
FS File: /sys_cal.html, size: 4.37KB
FS File: /sys_config.html, size: 1.51KB
FS File: /sys_info.html, size: 2.60KB
FS File: /sys_reboot.html, size: 1.60KB
FS File: /sys_update.html, size: 4.43KB
FS File: /catfeeder.log, size: 679B

Failed to open config filevoid AsyncFSWebServer::defaultConfig()
Failed to open secret file
void AsyncFSWebServer::configureWifiAP()
Setting AP configuration ...
AP Pass disabled
---Flash LED during 250 ms 3 times. Old state = 1
AP IP address = 192.168.1.1
MAC Addr: 84:0D:8E:B0:71:97
Open http://192.168.1.1/ to manage the CatFeeder
Flash chip size: 4194304
Scketch size: 544832
Free flash space: 1548288
HTTP server started

OTA Ready
END Setup
```

This errors are ok the first time:

```
CatFeeder: Failed to open config file /catfeeder.json
Failed to open config filevoid AsyncFSWebServer::defaultConfig()
```

The interesting lines are:

```
AP IP address = 192.168.1.1
MAC Addr: 84:0D:8E:B0:71:97
Open http://192.168.1.1/ to manage the CatFeeder
```

You have the mac address, if you need to add them to the Wifi MAC filter, and the configured IP for the AP (Access Point). 

These mean that the CatFeeder schedule configuration `/catfeeder.json` file is not found, and the WIFI configuration file `/config.json` hasn't been found too. This is due
that a fresh installation doesn't create this files, and force the CatFeeder to start as Access Point to enable configuration. The board starts in this mode if it can't found
the configuration files, or it can't connect to the configured WIFI (see `FSWebServerLib.h:27`, by default it waits 60 seconds `#define WIFI_CONNECT_TIMEOUT_TO_AP 60`).

# Configure CatFeeder

## Connect to the AP

The AP SSID if build using `CATF` and the CHIPID (e.g. `CATF1563415`). So search this WIFI in your device (e.g. mobile) and connect to this WIFI. Then point you web
brower to `http://192.168.1.1` and you should see something like the following:

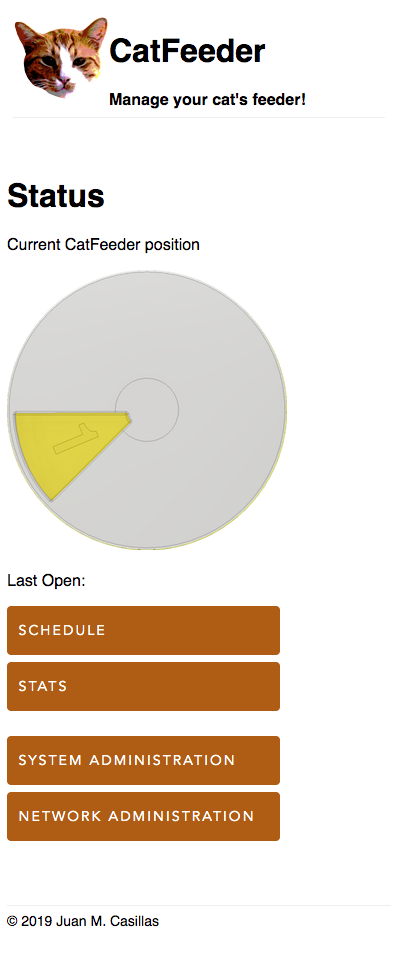
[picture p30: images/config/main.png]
Main Main Page


If you want to add the CatFeeder to your home network, do the following. Is not required to operate the CatFeeder, but it is easy to manage it. To add CatFeeder to your
home network, click on `Network Settings`

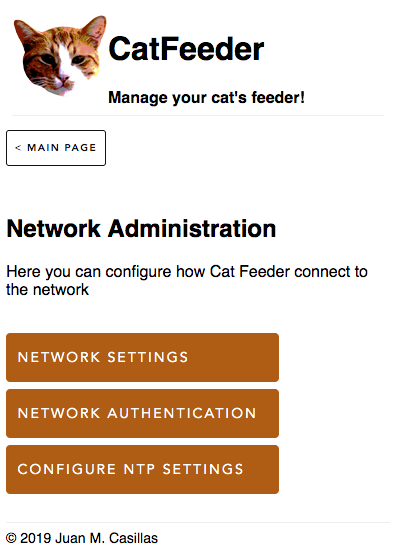
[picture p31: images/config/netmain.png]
Network Network Main Page


And now, configure the SSID, your password the IP for the CatFeeder (I suggest you not to use DHCP and put a high one, e.g. 250, and the gateway). Remember to add the
MAC address in your router table if your filter MAC addresses, *before* adding CatFeeder to the network. If everything goes fine, you should connect to your AP and
be able to ping the device from your home network. 

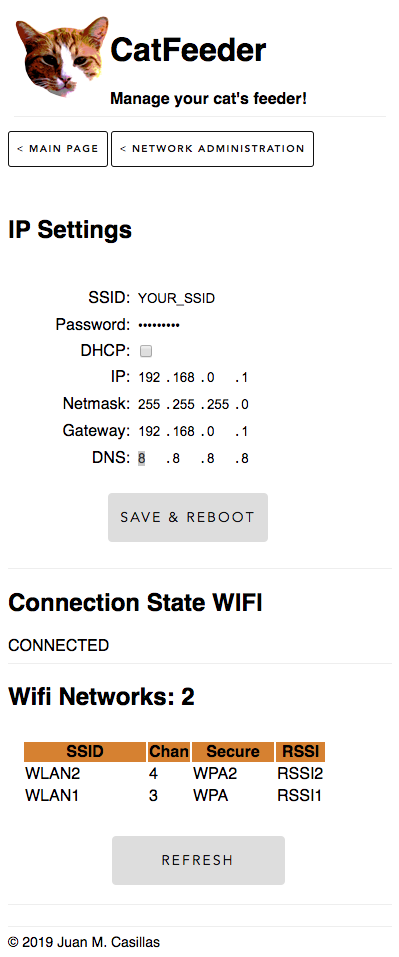
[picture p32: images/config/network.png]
Net Network Configuration


CatFeeder connects to NTP server to get the time. If you want to specify a nearby NTP server, go to Network Main Page, then click on NTP Settings and fill the following form:

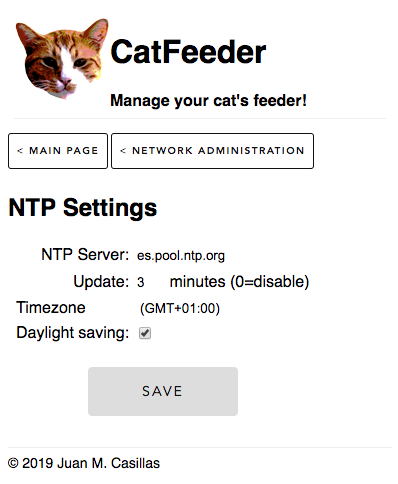
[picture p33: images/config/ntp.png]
NTP NTP configuration


# Using CatFeeder

## Calibration

First time you should calibrate it. After assembly it, the CatFeeder should be calibrated, but you can fine tune it. Go to System Administration, and click on `System Calibration`

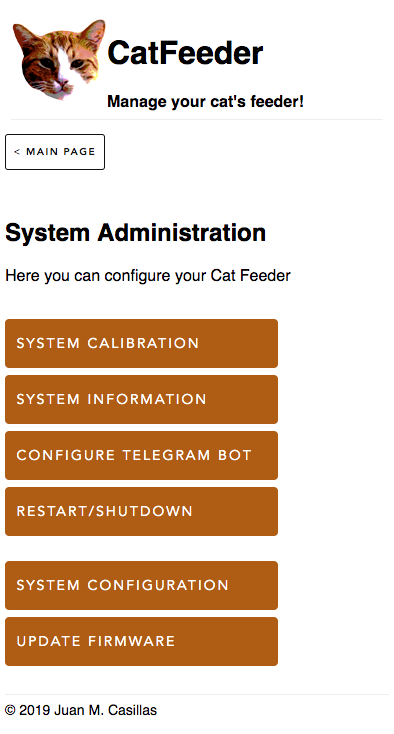
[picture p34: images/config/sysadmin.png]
SysAdmin System Administration


So in this window, use the arrows to move the cap so the slot 1 is open. Check the marks in the inner case and the cap so they are aligned (centered). 
Press `Start` when you're ready. After getting catfeeder calibrated, you can check in the bottom menu if the system moves to
the specific slot. After check it, press `Restore` to move the CatFeeder to the slot `#1`

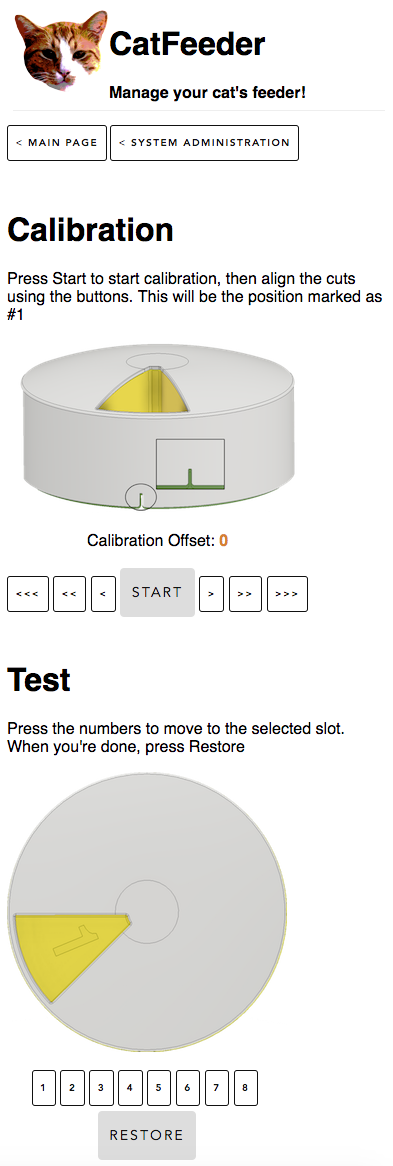
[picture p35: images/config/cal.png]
Calibration


## Configure schedules

In the main page, press `Schedule` button. CatFeeder has 8 slots, and 7 programs (the first slot is open, so you can leave it with food the first time to your pet, but this doesn't count as program.). The slot number and 
the programs are not related, but if everything starts on 1, it's easy and clear. Use the `Clear` button to clear one program, `Reset All` to clear all at once. To select when
the program run, just insert a date and a time using the calendar provided. Note that programs are run in time order, not in schedule order. When you're done, press `Save`. 
CatFeeder starts to work, and move to the next slot if it have a program. Easy. If you want to check the logs, click on `Stats` button in the main page.

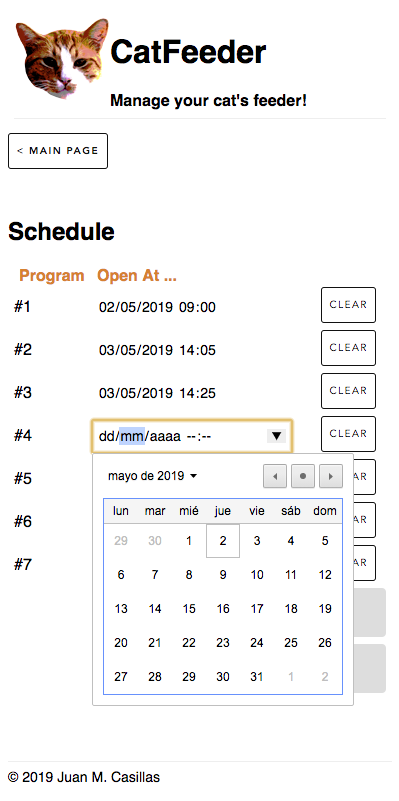
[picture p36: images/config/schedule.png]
Schedule


Hope you enjoy CatFeeder!

## Additional Notes

1. 28/October/2019 notes.
    1. I migrated from `ArduinoJson` 5 to 6, changing also the `FSBrowserNG` library.
    2. ESP8266 has a hard limit of 5 open files, so I merge all the CSS and the JS together, getting `all.min.css` and  `all.min.js`. This fixes the problem with error `500` in some cases, when retrieving too much files (e.g. scheduler)
    3. Fixed motor from 8 steps to 4 steps, changing the `_motor_move_to()` so it get the right slot.

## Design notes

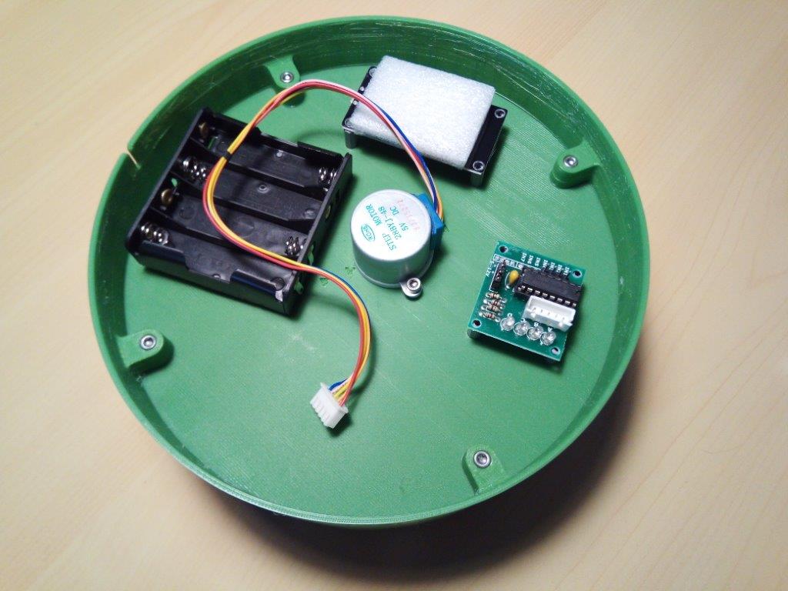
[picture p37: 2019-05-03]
images/electronics.jpg

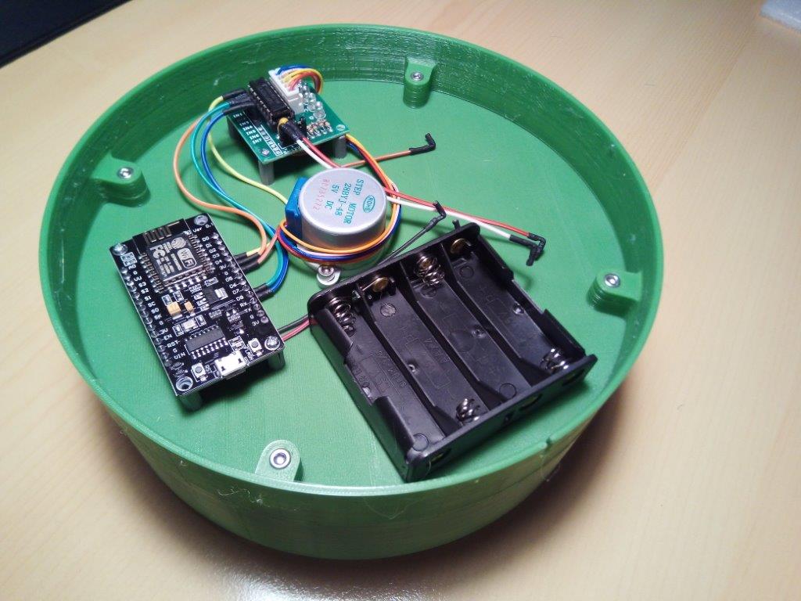
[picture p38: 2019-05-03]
images/electronics_2.jpg

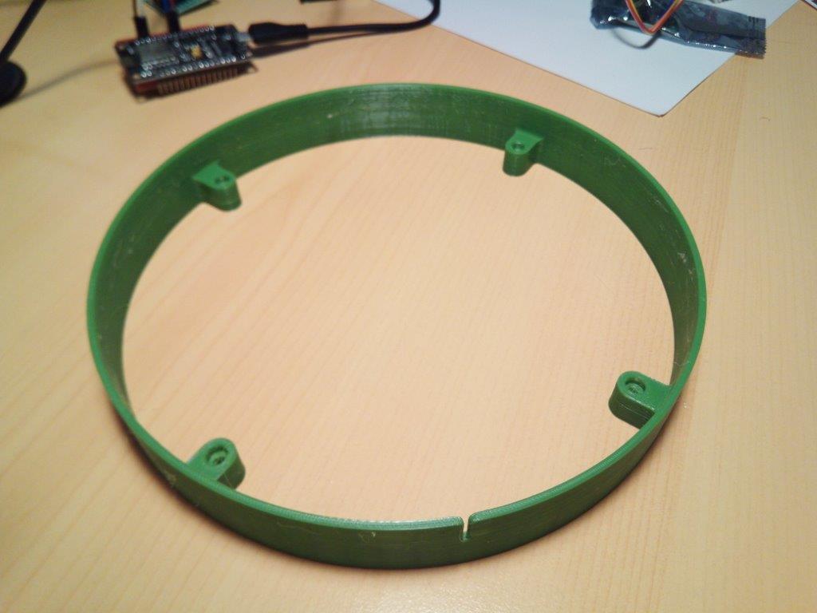
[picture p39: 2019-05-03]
images/base_top.jpg

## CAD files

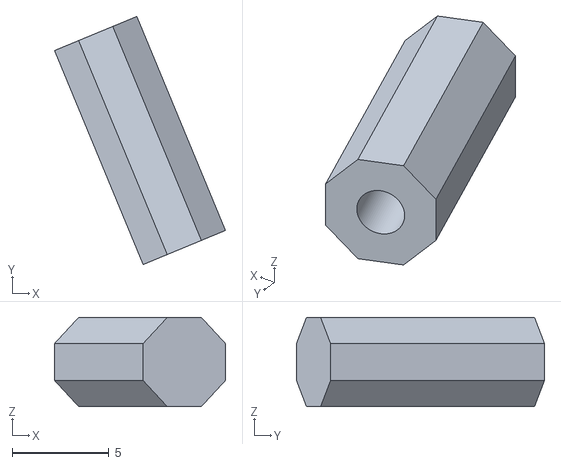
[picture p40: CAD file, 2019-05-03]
Hardware/3DPrinting/CatFeeder/8x_separator.stl
8.86 x 12.9 x 4.62

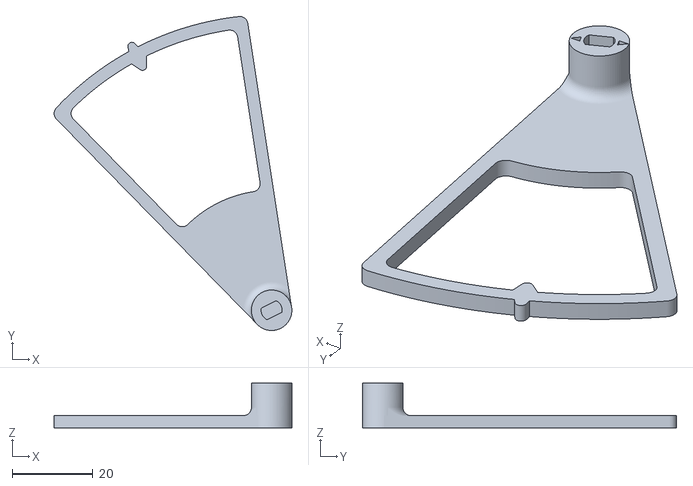
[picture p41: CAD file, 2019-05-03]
Hardware/3DPrinting/Prototype/upper.stl
58.7 x 77.6 x 11.0

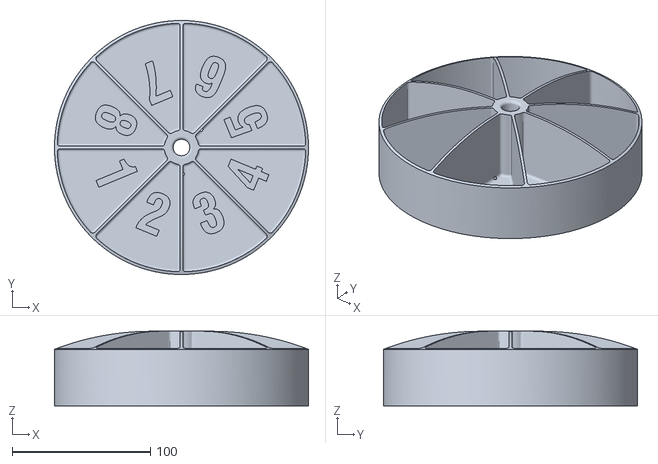
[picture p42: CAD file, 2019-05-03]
Hardware/3DPrinting/CatFeeder/1x_inner_case.stl
184.0 x 184.0 x 54.0

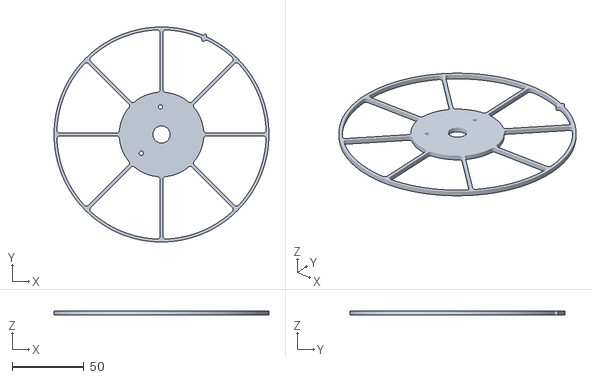
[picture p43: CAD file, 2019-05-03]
Hardware/3DPrinting/Prototype/floor.stl
150.0 x 150.0 x 3.00

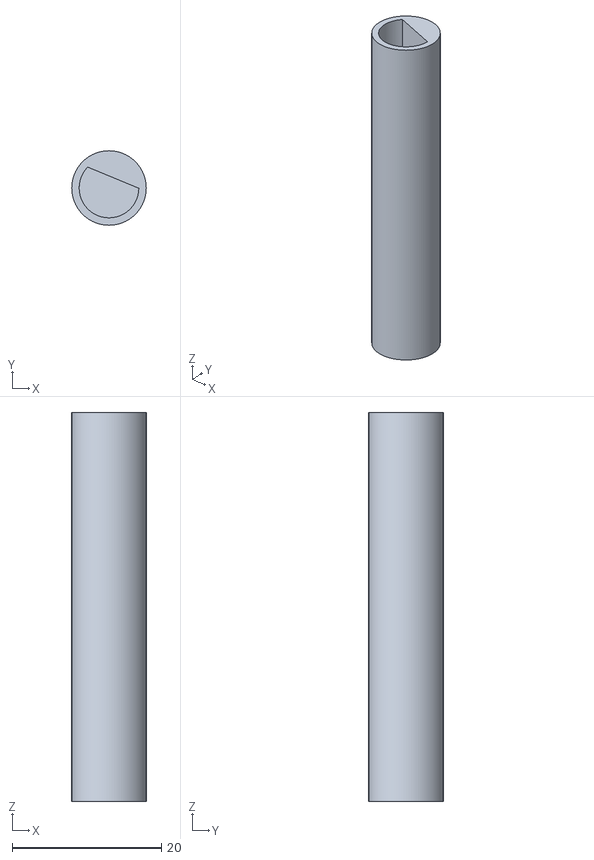
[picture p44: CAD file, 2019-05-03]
Hardware/3DPrinting/CatFeeder/1x_axis.stl
10.0 x 10.0 x 52.2

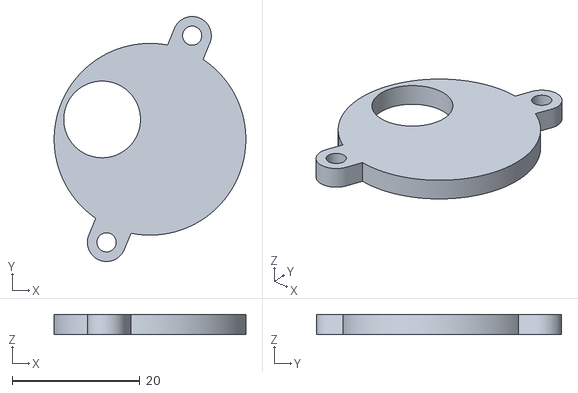
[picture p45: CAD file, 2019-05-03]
Hardware/3DPrinting/Prototype/motor_support.stl
30.0 x 38.3 x 3.20

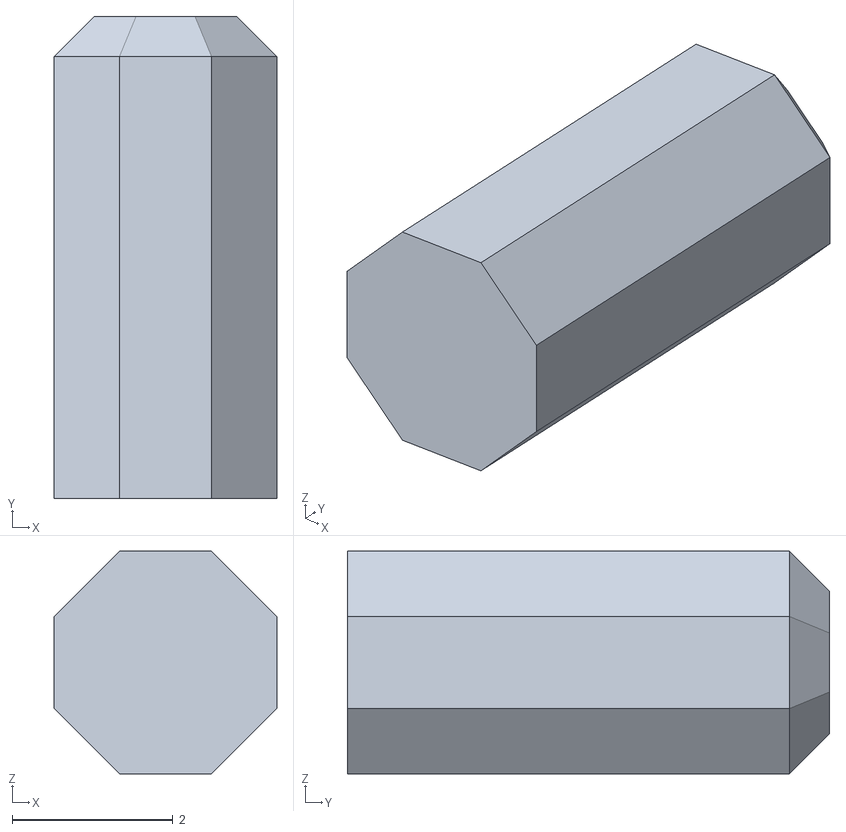
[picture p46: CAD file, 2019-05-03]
Hardware/3DPrinting/CatFeeder/2x_separator_battery.stl
2.77 x 6.00 x 2.77

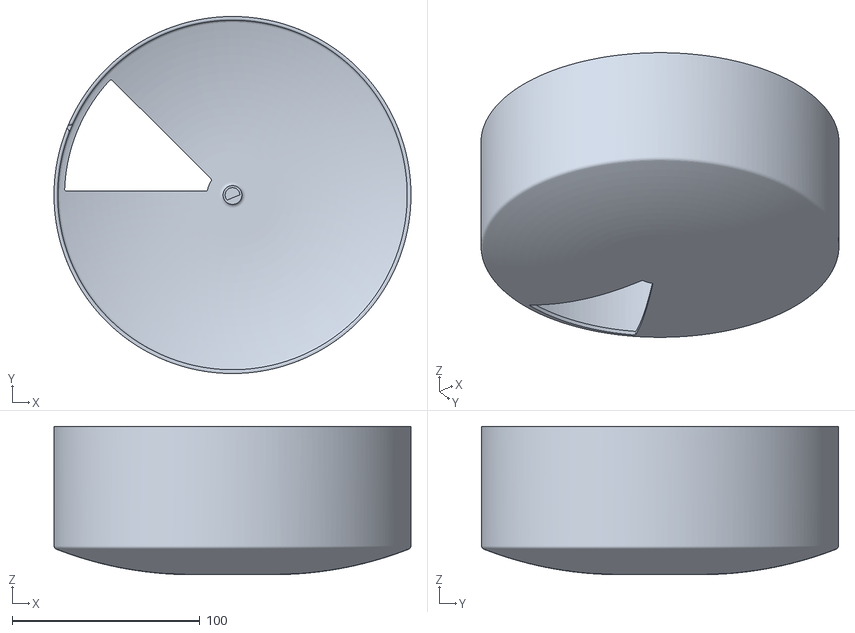
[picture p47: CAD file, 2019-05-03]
Hardware/3DPrinting/CatFeeder/1x_cap.stl
190.0 x 190.0 x 79.0

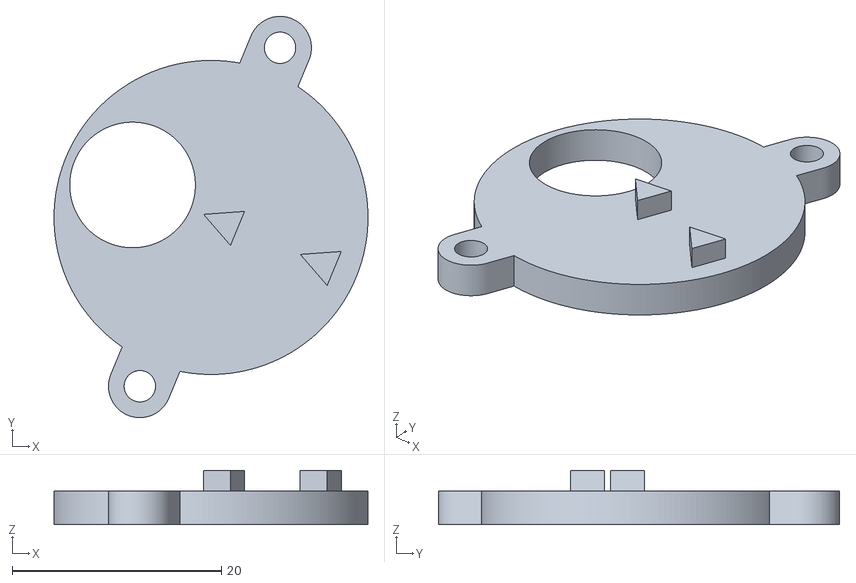
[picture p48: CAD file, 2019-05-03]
Hardware/3DPrinting/CatFeeder/1x_motor_support.stl
30.0 x 38.3 x 5.20

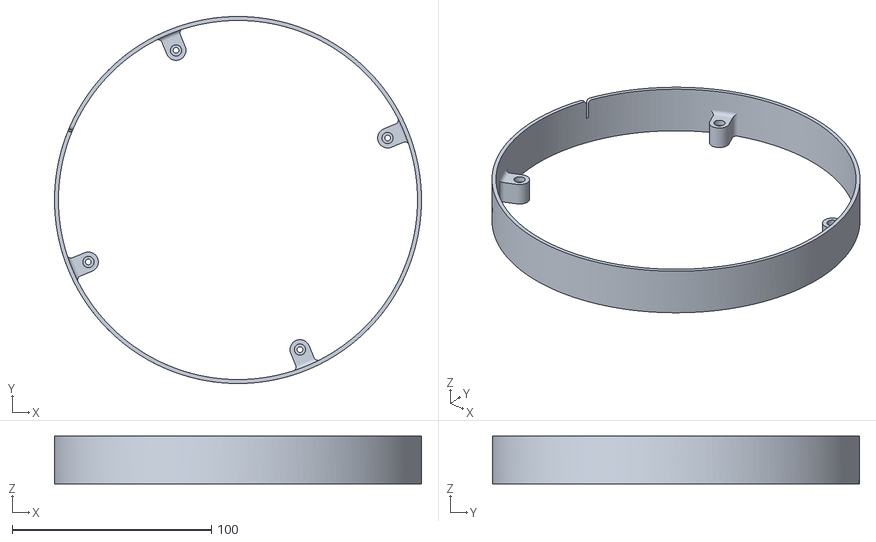
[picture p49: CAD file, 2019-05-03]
Hardware/3DPrinting/CatFeeder/1x_base.stl
184.0 x 184.0 x 24.0

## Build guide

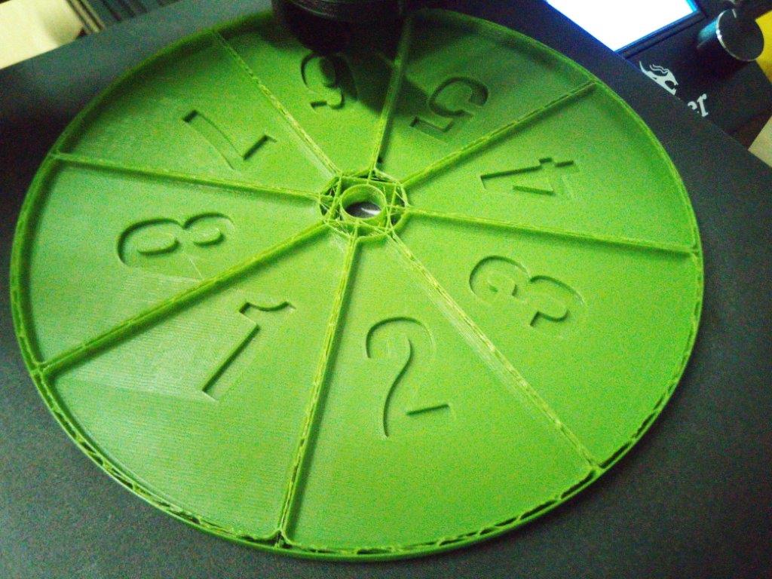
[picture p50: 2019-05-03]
images/inner_case_printing.jpg

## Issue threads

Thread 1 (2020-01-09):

Catfeeder is not coonecting with the wifi  router

tmmsunny012, 2020-01-09:
After trying to setup network the serial monitor does not show the SSID and Password. Also, it doesn't connect with my router. Before that happens it starts making the server. blow is the serial log -

191 JSON file size: 193 bytes
{
  "ip": [
    192,
    168,
    1,
    1
  ],
  "netmask": [
    255,
    255,
    255,
    0
  ],
  "gateway": [
    192,
    168,
    1,
    2
  ],
  "dns": [
    8,
    8,
    8,
    8
  ],
  "dhcp": false,
  "ntp": "es.pool.ntp.org",
  "NTPperiod": 15,
  "timeZone": 10,
  "daylight": true,
  "deviceName": "CatFeeder"
}Data initialized.
SSID:  PASS:
NTP Server: es.pool.ntp.org
bool AsyncFSWebServer::load_config()
Failed to open secret file
void AsyncFSWebServer::configureWifi()
bcn 0
del if1
mode : sta(a0:50:b3:6a:6c:29)
Connecting to
NO DHCP - Use static connection
MAC Addr: A0:50:B3:6A:6C:29
Open http://192.168.1.1/ to manage the CatFeeder
Flash chip size: 4194304
Scketch size: 444880
Free flash space: 1650688
HTTP server started

OTA Ready
END Setup

what should I do in that case? the esp8266 SDK 2.5 doesn't compile now with the new cat slot code. I am currently using 2.6.0 SDK  to solve that ..

Another question-
what version of Arduino you are using to compile your code?

juanmcasillas, 2020-01-09:
Lets see.
The config (config.json) file should look like:

```
{
"ssid":"WLAN_XXXX",
"pass":"XXXX",
"ip":[192,168,1,1],
"netmask":[255,255,255,0],
"gateway":[192,168,1,2],
"dns":8,8,8,8],
"dhcp":false,"ntp":"es.pool.ntp.org",
"NTPperiod":15,
"timeZone":10,
"daylight":true,
"deviceName":"CatFeeder"
}
```

Looks like the "ssid" and "pass" fields are not inside the config.json file.
Also, you're using 192.168.1.1 as CatFeeder IP and 192.168.1.2 for the router. Is this right?

Let's see some versions:

I use: ESP8266 by ESP8266 Community version 2.5.0
Arduino IDE: 1.8.10
Can you paste the compilation log, to check the errors?

Thank in advance,

tmmsunny012, 2020-01-12:
Hi Juanmcasillas/Catfeeder-Slot
thanks for coming back to me.
Unfortunately, the problem was not linked with any of this. The problem is
coming from SPIFFS. I just figured it by reading some blogs. I was using 2
MB FS with OTA 1019KB.. it was effecting the flash and unable to create a
config file. After I changed it to 3MB FS (OTA 512KB), it works perfectly
now.

Few questions I want to ask -
1. I saw that if the Esp8266 goes off the scheduler time values are gone.
Is that normal?
2. I have designed a feeder that has a screw that takes out food from
the reservoir. Instead of making it slot, I did this process. In that case
which part of the codes should change? A few suggestions might help as I
not that advanced coder like you.
3. For my screw type cat feeder, I don't need a date data(DD-MM-YY) to feed
the cat. Instead of that, I need ESP to act as a daily alarm(only time
HH:MM: SS  is needed) where every day at a certain time it will trigger.
Any suggestions on how to do that?

you have done an awesome job btw.

On Thu, 9 Jan 2020 at 18:46, Juan M. Casillas <notifications@github.com>
wrote:

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

juanmcasillas, 2020-01-12:
> Hi Juanmcasillas/Catfeeder-Slot thanks for coming back to me. Unfortunately, the problem was not linked with any of this. The problem is coming from SPIFFS. I just figured it by reading some blogs. I was using 2 MB FS with OTA 1019KB.. it was effecting the flash and unable to create a config file. After I changed it to 3MB FS (OTA 512KB), it works perfectly now.

I forget to mention that. You need at least 2 MB FS to get the thing works :-)
Glad to hear that works for you.

> Few questions I want to ask - 1. I saw that if the Esp8266 goes off the scheduler time values are gone. Is that normal?

Yes, These boards doesn't include a RTC (Real Time Clock). These tiny (an cheap) devices, backup the state with a battery (usually CR 3022) and they avoid to lose the time when the microcontroller lost the power. These breakout boards are easy to integrate (usually they "speak" I2C). See for more info:

* [Adafruit breakout RTC boards](https://learn.adafruit.com/ds1307-real-time-clock-breakout-board-kit/overview)
* [Adafruit RCTLib](https://github.com/adafruit/RTClib)

I use NTP sync to keep the time "uptime". So you don't need to worry about losing the time. But if you need more robust time control, get a RTC breakout board and integrate it.

> 2. I have designed a feeder that has a screw that takes out food from the reservoir. Instead of making it slot, I did this process. In that case which part of the codes should change? A few
suggestions might help as I not that advanced coder like you.

CatFeeder-Slot works in this way (pseudocode).

```
For Each second
     If time == Scheduled Time:
          move_to_next_slot
```

If you need to configure it for your needs, you have modify some code. See [catfeeder.cpp](https://github.com/juanmcasillas/CatFeeder-Slot/blob/a2ddf2b0ec7ac58a84a16a1a2fc8b5fbfb80183f/Software/catfeedercircular/catfeeder.cpp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)

```c++
void CatFeederClass::CheckScheduler(void *arg) {
    // USE self instead of this
    // this function is called each CatFeederClass::SCHEDULE_PERIOD (1 second)
    CatFeederClass *self = reinterpret_cast<CatFeederClass *>(arg);

    int programs = self->getPROGRAMS();
    unsigned long mystamp,prgstamp;

    String mytime = self->GetTimeStampNow();
    mystamp = self->ToTimestamp(mytime);

    for (int i=0; i< programs; i++) {
        String sched = self->getScheduler(i);
        if (sched != "") {
            prgstamp = self->ToTimestamp(sched);
  
            if (mystamp == prgstamp) {
                // do things if matches
                DEBUGLOG(" TICK_MATCH! #%d %s %s\n", i, mytime.c_str(), sched.c_str());
                 self->setLastOpen(sched.c_str());
                 //self->AdvanceSlot();
                // CALL HERE THE CODE TO MOVE THE MOTOR:

            }
        }
    }
}
```

You should modify the `_motor_moveto()` code to do whatever you want (e.g. turn 3 times, etc).
see [catfeeder.cpp](https://github.com/juanmcasillas/CatFeeder-Slot/blob/a2ddf2b0ec7ac58a84a16a1a2fc8b5fbfb80183f/Software/catfeedercircular/catfeeder.cpp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).

```c++

// calls to function Move()
// dir: 0, 1
// steps: number of steps to move
// _motor is the motor stepper implementation
// you have to call the function in this way, to avoid blocking
schedule_function(std::bind(MotorStepperClass::Move, dir, steps, _motor));
```

> 3. For my screw type cat feeder, I don't need a date data(DD-MM-YY) to feed the cat. Instead of that, I need ESP to act as a daily alarm(only time HH:MM: SS is needed) where every day at a certain time it will trigger.

See [catfeeder.cpp](https://github.com/juanmcasillas/CatFeeder-Slot/blob/a2ddf2b0ec7ac58a84a16a1a2fc8b5fbfb80183f/Software/catfeedercircular/catfeeder.cpp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) and change the function to this:

```c++
String CatFeederClass::GetTimeStampNow() {
    time_t t = now();
    char *buf = (char *)malloc(1024);
    sprintf(buf, "%02d:%02d:%02d", hour(t), minute(t), second(t));
    String ret = buf;
    free(buf);
    return(ret);
}
```

See [catfeeder.cpp](https://github.com/juanmcasillas/CatFeeder-Slot/blob/a2ddf2b0ec7ac58a84a16a1a2fc8b5fbfb80183f/Software/catfeedercircular/catfeeder.cpp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) and  the function in order to use only the hour, minute second, as these:

```c++
unsigned long CatFeederClass::ToTimestamp(String d) {
    // EPOCH 01/01/1970 00:00:00
    // 1 hour	3600 seconds
    // 1 day	86400 seconds
    // 1 week	604800 seconds
    // 1 month (30.44 days) 	2629743 seconds
    // 1 year (365.24 days) 	 31556926 seconds

    int hour, minute, second;

    sscanf(d.c_str(),"%02d:%02d:%02d", &hour, &minute, &second);

    unsigned long ret;

    ret =  (hour * 3600) + (minute * 60) + second;

    return(ret);
}
```

> Any suggestions on how to do that? you have done an awesome job btw.

Hope it works for you :-)
Kind Regards

tmmsunny012, 2020-01-25:
Sorry for replying to you so late. It took me long to figure out most of the codes.  I have followed your steps and its kinda solve the issues. regarding the Telegram bot library. I couldn't find any code inside the catfeeder.cpp or cat feeder.h ..if I want to implement telegram bot where should I look for it in the codes. A few suggestions might help me a bit. Thanks again.

:)

juanmcasillas, 2020-01-26:
> Sorry for replying to you so late. It took me long to figure out most of the codes. I have followed your steps and its kinda solve the issues. regarding the Telegram bot library. I couldn't find any code inside the catfeeder.cpp or cat feeder.h ..if I want to implement telegram bot where should I look for it in the codes. A few suggestions might help me a bit. Thanks again.
>
> :)

Telegram bot is in very preliminary support, but you shouldn't have any problems working
with it. For this reason, I remove it from the latest development release. If you wanna know
more about it, just clone the version `64e54b5e32a5e0781db92c703e64fabb9f1622d1`
(initial release) this version has the code with the preliminary support.

Also check  my [Universal Telegram Bot](https://github.com/juanmcasillas/Universal-Arduino-Telegram-Bot) fork.

Thanks in advance,

tmmsunny012, 2020-01-28:
Hi ,I copied the source files for running into telegram .It seems the the telegram bot you forked and changed for Json 6 is not compiling so far . I tried some changes and it compiles but not running  the bot. I saw this in the bot.h .Do I need change bool _active =true ??
I did that and the esp  started to crash.

I am attaching the modified bot codes for json 6

 here.May be you can look into this .

```
`/*

*/

#ifndef UniversalTelegramBot_h
#define UniversalTelegramBot_h

#include <Arduino.h>
#include <ArduinoJson.h>
#include <Client.h>

#define HOST "api.telegram.org"
#define SSL_PORT 443
#define HANDLE_MESSAGES 1
#define SEND_DELAY 1000
#define RCV_DELAY 1000

typedef bool (*MoreDataAvailable)();
typedef byte (*GetNextByte)();

struct telegramMessage {
  String text;
  String chat_id;
  String chat_title;
  String from_id;
  String from_name;
  String date;
  String type;
  float longitude;
  float latitude;
  int update_id;
};

class UniversalTelegramBot {
public:
  UniversalTelegramBot(String token, Client &client);
  String sendGetToTelegram(String command);
  String sendPostToTelegram(String command, JsonObject &payload);
  String
  sendMultipartFormDataToTelegram(String command, String binaryProperyName,
                                  String fileName, String contentType,
                                  String chat_id, int fileSize,
                                  MoreDataAvailable moreDataAvailableCallback,
                                  GetNextByte getNextByteCallback);

  bool getMe();

  bool sendSimpleMessage(String chat_id, String text, String parse_mode);
  bool sendMessage(String chat_id, String text, String parse_mode = "");
  bool sendMessageWithReplyKeyboard(String chat_id, String text,
                                    String parse_mode, String keyboard,
                                    bool resize = false, bool oneTime = false,
                                    bool selective = false);
  bool sendMessageWithInlineKeyboard(String chat_id, String text,
                                     String parse_mode, String keyboard);

  bool sendChatAction(String chat_id, String text);

  bool sendPostMessage( JsonObject &payload);
  String sendPostPhoto(JsonObject &payload);
  String sendPhotoByBinary(String chat_id, String contentType, int fileSize,
                           MoreDataAvailable moreDataAvailableCallback,
                           GetNextByte getNextByteCallback);
  String sendPhoto(String chat_id, String photo, String caption = "",
                   bool disable_notification = false,
                   int reply_to_message_id = 0, String keyboard = "");
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

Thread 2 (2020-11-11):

Error on compile

jota-f, 2020-11-11:
Helo! I get de error bellow

Arduino: 1.8.12 (Windows 10), Placa:"WeMos D1 R2 & mini, 80 MHz, 4M (1M SPIFFS), v2 Lower Memory, Disabled, None, Only Sketch, 921600"

sketch\catfeeder.cpp: In member function 'String CatFeederClass::Calibrate(AsyncWebServerRequest*)':

catfeeder.cpp:138:74: error: 'schedule_function' was not declared in this scope

     schedule_function(std::bind(MotorStepperClass::Move, mult, s, _motor));

                                                                          ^

sketch\catfeeder.cpp: In member function 'void CatFeederClass::_motor_moveto(int, int)':

catfeeder.cpp:576:77: error: 'schedule_function' was not declared in this scope

     schedule_function(std::bind(MotorStepperClass::Move, dir, steps, _motor));

                                                                             ^

Foram encontradas múltiplas bibliotecas para "Servo.h"
Usado: C:\Users\snipe\AppData\Local\Arduino15\packages\esp8266\hardware\esp8266\2.4.1\libraries\Servo
Não usado: C:\Program Files (x86)\Arduino\libraries\Servo
Foram encontradas múltiplas bibliotecas para "ArduinoJson.h"
Usado: C:\Users\snipe\Documents\Arduino\libraries\ArduinoJson
Não usado: C:\Users\snipe\Documents\Arduino\libraries\arduino_406825
exit status 1
'schedule_function' was not declared in this scope

juanmcasillas, 2020-11-12:
Hello,

I try to compile it with 1.8.11

 Used: /Users/assman/Library/Arduino15/packages/esp8266/hardware/esp8266/2.5.0/libraries/Servo
 Not used: /Applications/Arduino.app/Contents/Java/libraries/Servo
Using library ESP8266WiFi at version 1.0 in folder: /Users/assman/Library/Arduino15/packages/esp8266/hardware/esp8266/2.5.0/libraries/ESP8266WiFi
Using library Time at version 1.5 in folder: /Archive/Src/Arduino/libraries/Time
Using library NtpClient at version 2.5.1 in folder: /Archive/Src/Arduino/libraries/NtpClient
Using library ESPAsyncTCP at version 1.2.0 in folder: /Archive/Src/Arduino/libraries/ESPAsyncTCP
Using library ESPAsyncWebServer at version 1.2.3 in folder: /Archive/Src/Arduino/libraries/ESPAsyncWebServer
Using library Hash at version 1.0 in folder: /Users/assman/Library/Arduino15/packages/esp8266/hardware/esp8266/2.5.0/libraries/Hash
Using library ESP8266mDNS at version 1.2 in folder: /Users/assman/Library/Arduino15/packages/esp8266/hardware/esp8266/2.5.0/libraries/ESP8266mDNS
Using library Ticker at version 1.0 in folder: /Users/assman/Library/Arduino15/packages/esp8266/hardware/esp8266/2.5.0/libraries/Ticker
Using library ArduinoOTA at version 1.0 in folder: /Users/assman/Library/Arduino15/packages/esp8266/hardware/esp8266/2.5.0/libraries/ArduinoOTA
Using library ArduinoJson at version 6.11.3 in folder: /Archive/Src/Arduino/libraries/ArduinoJson
Using library FSBrowserNG at version 1.0.0 in folder: /Archive/Src/Arduino/libraries/FSBrowserNG
Using library Servo at version 1.0.2 in folder: /Users/assman/Library/Arduino15/packages/esp8266/hardware/esp8266/2.5.0/libraries/Servo
/Users/assman/Library/Arduino15/packages/esp8266/tools/xtensa-lx106-elf-gcc/2.5.0-3-20ed2b9/bin/xtensa-lx106-elf-size -A /var/folders/cc/0xwh_8tn7xdf8834vtcvvlt00000gn/T/arduino_build_213962/catfeedercircular.ino.elf
Sketch uses 425324 bytes (40%) of program storage space. Maximum is 1044464 bytes.
Global variables use 37408 bytes (45%) of dynamic memory, leaving 44512 bytes for local variables. Maximum is 81920 bytes.

It works.

my board version: esp32 1.0.2

Also, I test with the latest arduino IDE (1.8.13) and it works, too. Check your ESP32 Library.

Using library ESP8266WiFi at version 1.0 in folder: /Users/assman/Library/Arduino15/packages/esp8266/hardware/esp8266/2.5.0/libraries/ESP8266WiFi
Using library Time at version 1.5 in folder: /Archive/Src/Arduino/libraries/Time
Using library NtpClient at version 2.5.1 in folder: /Archive/Src/Arduino/libraries/NtpClient
Using library ESPAsyncTCP at version 1.2.0 in folder: /Archive/Src/Arduino/libraries/ESPAsyncTCP
Using library ESPAsyncWebServer at version 1.2.3 in folder: /Archive/Src/Arduino/libraries/ESPAsyncWebServer
Using library Hash at version 1.0 in folder: /Users/assman/Library/Arduino15/packages/esp8266/hardware/esp8266/2.5.0/libraries/Hash
Using library ESP8266mDNS at version 1.2 in folder: /Users/assman/Library/Arduino15/packages/esp8266/hardware/esp8266/2.5.0/libraries/ESP8266mDNS
Using library Ticker at version 1.0 in folder: /Users/assman/Library/Arduino15/packages/esp8266/hardware/esp8266/2.5.0/libraries/Ticker
Using library ArduinoOTA at version 1.0 in folder: /Users/assman/Library/Arduino15/packages/esp8266/hardware/esp8266/2.5.0/libraries/ArduinoOTA
Using library ArduinoJson at version 6.11.3 in folder: /Archive/Src/Arduino/libraries/ArduinoJson
Using library FSBrowserNG at version 1.0.0 in folder: /Archive/Src/Arduino/libraries/FSBrowserNG
Using library Servo at version 1.0.2 in folder: /Users/assman/Library/Arduino15/packages/esp8266/hardware/esp8266/2.5.0/libraries/Servo
/Users/assman/Library/Arduino15/packages/esp8266/tools/xtensa-lx106-elf-gcc/2.5.0-3-20ed2b9/bin/xtensa-lx106-elf-size -A /var/folders/cc/0xwh_8tn7xdf8834vtcvvlt00000gn/T/arduino_build_971435/catfeedercircular.ino.elf
Sketch uses 425324 bytes (40%) of program storage space. Maximum is 1044464 bytes.
Global variables use 37408 bytes (45%) of dynamic memory, leaving 44512 bytes for local variables. Maximum is 81920 bytes.

Use the repo from here: https://github.com/juanmcasillas/CatFeeder-Slot.git <https://github.com/juanmcasillas/CatFeeder-Slot.git>

If you need more support, please tell me.

Kind Regards,

Juan M. Casillas

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

jota-f, 2020-11-13:
Updated the ide to 1.8.13
esp32 library for 1.0.2 and esp8266 for 2.7.4 and now it works!
Thank you.
One more question:
is it possible to change the webserver port? so that I can route on my router and not be without internet access in the whole house?

juanmcasillas, 2020-11-13:
Hello !

Glad to read good news! :-)

> is it possible to change the webserver port? so that I can route on my router and not be without internet access in the whole house?
>
For sure, but you have to edit  the FSWebServerLib.cpp file (in FSBrowserNG library). (FSBrowserNG/src/FSWebServerLib.cpp)

Look for this AsyncFSWebServer ESPHTTPServer(80);
and change 80 to your port.

Kind Regards,

Juan M. Casillas

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

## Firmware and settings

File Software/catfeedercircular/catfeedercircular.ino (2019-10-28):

#include <ESP8266WiFi.h>
#include <FS.h>
#include <WiFiClient.h>
#include <TimeLib.h>
#include <NtpClientLib.h>
#include <ESPAsyncTCP.h>
#include <ESPAsyncWebServer.h>
#include <ESP8266mDNS.h>
#include <Ticker.h>
#include <ArduinoOTA.h>
#include <ArduinoJson.h>
#include <FSWebServerLib.h>
#include <Hash.h>


#include "catfeeder.h"

// CatFeeder variable /////////////////////////////////////////////////////////

CatFeederClass CATFEEDER;

// include the callback code //////////////////////////////////////////////////

#include "callback.h"

/// ARDUINO BLOCK /////////////////////////////////////////////////////////////

void setup() {
    
    // configure CatFeeder Objects
    SPIFFS.begin();
    CATFEEDER.begin(&SPIFFS);

    // configure custom handlers first
    
    ESPHTTPServer.set_usercallbackfilter("/catfeeder");
    ESPHTTPServer.setUSERCallback(callbackFeeder);
    
    // WiFi is started inside library
    // Not really needed, checked inside and started if needed
    
    ESPHTTPServer.begin(&SPIFFS);
   
    // configure the logger to be served statically
    // maybe all the static elements in the directory
    // should be handled in this way.
    ESPHTTPServer.serveStatic("/catfeeder.log", SPIFFS, "/catfeeder.log");


    CATFEEDER.IsRunning();
    /* add setup code here */
}

/// MAIN LOOP /////////////////////////////////////////////////////////////////

void loop() {
    /* add main program code here */

    // DO NOT REMOVE. Attend OTA update from Arduino IDE
    ESPHTTPServer.handle();	
    
    //if (CATFEEDER.isBotActive()) {
    //    CATFEEDER.RunBot();
    //}
}

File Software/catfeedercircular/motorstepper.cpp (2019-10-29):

///////////////////////////////////////////////////////////////////////////////
/// STEPPER MOTOR Adapter /////////////////////////////////////////////////////
///////////////////////////////////////////////////////////////////////////////

#include "motorstepper.h"

void MotorStepperClass::begin() {
    pinMode(this->motorPin1, OUTPUT);
    pinMode(this->motorPin2, OUTPUT);
    pinMode(this->motorPin3, OUTPUT);
    pinMode(this->motorPin4, OUTPUT);
}

void MotorStepperClass::Clockwise() {

  this->_set_output(this->stepCounter);
  delay(this->motorSpeed);


  this->stepCounter++;
  if (this->stepCounter >= this->numSteps) this->stepCounter = 0;

  
}
 
void MotorStepperClass::Anticlockwise() {
  this->stepCounter--;
  if (this->stepCounter < 0) this->stepCounter = this->numSteps - 1;
  
  this->_set_output(this->stepCounter);
  delay(this->motorSpeed);


}
 
void MotorStepperClass::_set_output(int step) {
  digitalWrite(this->motorPin1, bitRead(this->stepsLookup[step], 0));
  digitalWrite(this->motorPin2, bitRead(this->stepsLookup[step], 1));
  digitalWrite(this->motorPin3, bitRead(this->stepsLookup[step], 2));
  digitalWrite(this->motorPin4, bitRead(this->stepsLookup[step], 3));
}

// static implementation overloading stepCounter.
void MotorStepperClass::Move(int counter, int steps, MotorStepperClass *motor) {
  for (int i=0; i< steps; i++) {
    if (counter == 1) motor->Clockwise();
    else motor->Anticlockwise();
  }
}

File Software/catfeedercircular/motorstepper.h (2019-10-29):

///////////////////////////////////////////////////////////////////////////////
/// STEPPER MOTOR Adapter /////////////////////////////////////////////////////
///////////////////////////////////////////////////////////////////////////////

#ifndef __MOTORSTEPPERCLASS_H__
#define __MOTORSTEPPERCLASS_H__

#include <Arduino.h>
#include <Servo.h>

#ifndef DBG_OUTPUT_PORT
#define DBG_OUTPUT_PORT Serial
#endif 

#ifndef RELEASE
#define DEBUGLOG(...) DBG_OUTPUT_PORT.printf(__VA_ARGS__)
#else
#define DEBUGLOG(...)
#endif



class MotorStepperClass {
    public:
        int stepsPerRev = 4096;  // pasos para una vuelta completa
        //int stepsPerRev = 4076;  // pasos para una vuelta completa
        const int numSteps = 4;
    protected:
        // motor: 28BYJ48
        // driver ULN2003
        //                             ESP8266           ULN2003 COLOR
        const int motorPin1 = D1;   // D1  (GPIO14)      IN1     black 
        const int motorPin2 = D2;   // D2  (GPIO12)      IN2     white 
        const int motorPin3 = D5;   // D5  (GPIO13)      IN3     Blue  
        const int motorPin4 = D6;   // D6  (GPIO15)      IN4     Red 
        
        int motorSpeed =  5;      // variable para fijar la velocidad milis
        int stepCounter = 0;     // contador para los pasos
        
        
        //tablas con la secuencia de encendido (descomentar la que necesiteis)
        //secuencia 1-fase
        //const int numSteps = 4;
        //const int stepsLookup[4] = { B1000, B0100, B0010, B0001 };
        
        //secuencia 2-fases
        
        const int stepsLookup[4] = { B1100, B0110, B0011, B1001 };
        
        //secuencia media fase
        //const int numSteps = 8;
        //const int stepsLookup[8] = { B1000, B1100, B0100, B0110, B0010, B0011, B0001, B1001 };
    
    public:
        void begin();
        void Clockwise();
        void Anticlockwise();
        static void Move(int counter, int steps, MotorStepperClass *motor);

    protected:

       void _set_output(int step);
};



#endif

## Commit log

2019-05-03 First public release of CatFeeder-Slot
    [1x_axis.stl, 1x_base.stl, 1x_cap.stl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]
2019-10-28 Migrated from ArduinoJson5 to ArduinoJSon6 Fixed the hard limit of 5 open files. I merged all the css and the js together, now I have all.min.js and all.min.css. This fixes the 500 HTTP error when tr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
    [catfeeder.cpp, catfeedercircular.ino, motorstepper.h]
2019-10-29 Fixed some bug I wrote this morning about to change to a servo motor
    [catfeeder.cpp, motorstepper.cpp, motorstepper.h]
